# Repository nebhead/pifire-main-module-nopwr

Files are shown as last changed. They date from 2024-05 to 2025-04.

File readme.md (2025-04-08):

# PiFire Main Module PCB (v4.x.x) KiCad Files

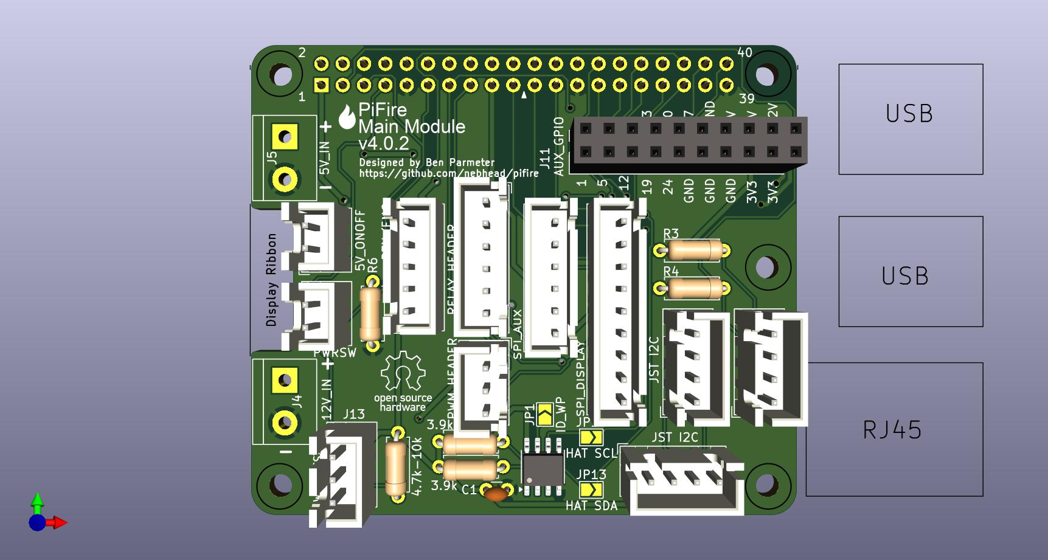
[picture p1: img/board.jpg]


## What is this? 

This PCB provides a modular approach to building your PiFire Smart Smoker Controller.  This board breaks out the many interfaces that are commonly used to support sensors, relays, displays and other devices.  This design allows the user to choose features that suit their needs such as using a PWM DC Fan instead of the AC fan system, or allows for different and expanded probe devices.  Some other notable features are the addition of a 1-Wire bus connector, a wake/shutdown option, and more!  

__Important Notes:__  
1. This board requires v1.8.x of PiFire or later.  As of May 2024, this version is still in development and can be tested by switching to the development branch in the updater page.  Ensure you run through the configuration wizard to select the v4.x.x board and configure your specific settings appropriately. 
1. This board does NOT support the selector switch to run in parallel with the OEM controller.  The pin used for this purpose has been repurposed for the wake/shutdown feature. 

The design intent for this board was to make a DIY accessible PCB that can be more easily put together by the maker/enthusiast of almost any skill level.  Full size components are used in most cases and most (if not all) parts should be readily available to order online.  See the [Interactive BOM](#interactive-bom) for more details about the parts used and links to order.

### What is PiFire? 

PiFire is a SBC based Pellet Smoker Controller.  More details can be found [here](https://nebhead.github.io/PiFire) or [at the GitHub repo](https://github.com/nebhead/pifire). 

## What's in this Repository?

### KiCad Project Files 
In this repository you will find the latest KiCad design files for the  PCB.  Simply load the project file (.kicad_pro) into the KiCad software and you should be able to edit as needed.  Or if you just want to get this board made, jump to the production section below.

### Interactive BOM

There is an interactive BOM located in the [/bom](bom/) folder which details the parts and provides some pin information as well.  Use this to gather the components you may need to build this board out and refer back to it for placement help.    

[BOM + Pin Info](https://nebhead.github.io/pifire-main-module-nopwr)

_This is a standalone HTML file that was autogenerated by the excellent plugin for KiCad. See the plugin here: [https://github.com/openscopeproject/InteractiveHtmlBom](https://github.com/openscopeproject/InteractiveHtmlBom)_

### PDF of the Schematic

Preview the schematic in PDF format here: [Schematic](schematic.pdf)

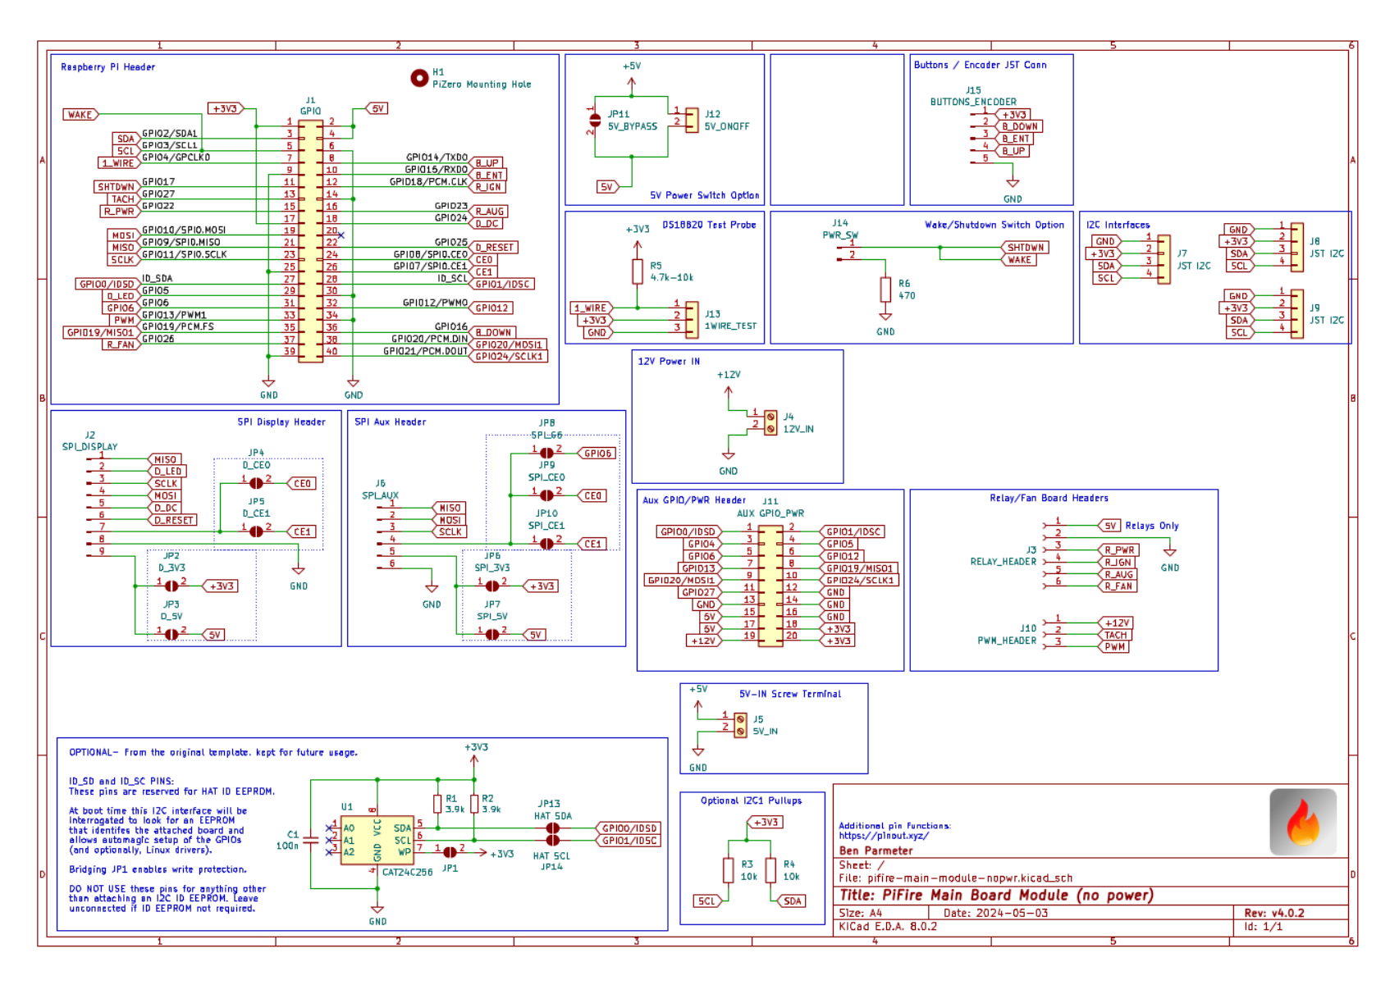
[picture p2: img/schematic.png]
Schematic PNG


### JLCPCB Production Files

If you wish to get these PCBs made by JLCPCB, the production files are provided in the `/production` folder.  For convenience, the file `production.zip` can simply be uploaded to JLCPCB to make it super easy to order boards.

Drop the zip file onto the order page, wait for it to upload then simply continue to order the board.  Optionally, select different board color, PCB quantity, surface finish, etc.  Most of the default settings should be sufficient. 

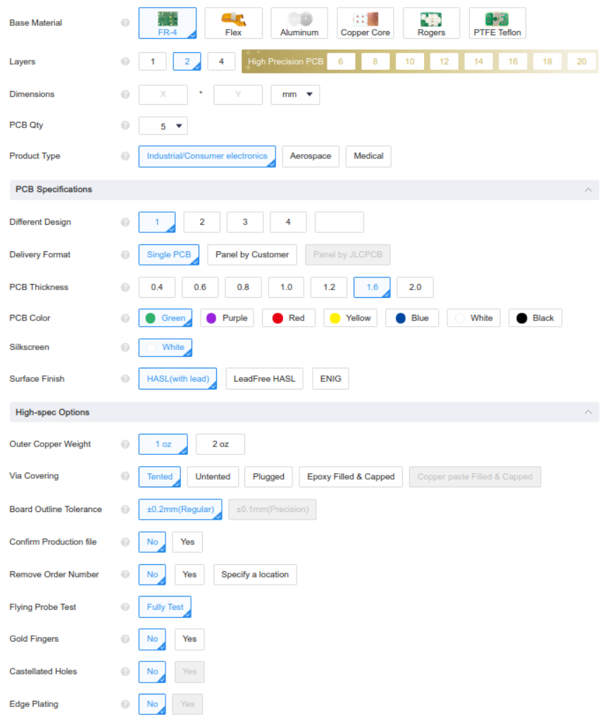
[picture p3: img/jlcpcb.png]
JLCPCB Order Page


### Links to the PCBs in this family of PiFire Boards

This PCB is part of a family of PCBs that can be used together to create  a full PiFire system.  Generally speaking you need the Main Module/Board, a Relay Control Board and a Probe Device board to have a basic PiFire system.  

**Main Module/Board** (required)
* [Main Board v4.0.x](https://github.com/nebhead/pifire-main-module-nopwr)

**Relay/Fan Control Boards** (choose one)
* [Mechanical Relay Module](https://github.com/nebhead/pifire-relay-module)
* [Solid State Relay Module](https://github.com/nebhead/pifire-relay-module-SSR)
* [Solid State Relay + PWM Fan Module](https://github.com/nebhead/pifire-relay-pwm-module-ssr) - Original Design
* [Solid State Relay + PWM Fan Module Alternate](https://github.com/nebhead/pifire-relay-pwm-module-ssr-alt) - Updated Design (Designed with help from @labmonkeyrat on Discord)

**Probe Device Board** (optional)
* [ADS Board](https://github.com/nebhead/pifire-ads-board) 

### General 4.x.x PCB Architecture

Sometimes it is easier to understand how a project is built out by looking at the general architecture.  I've created a high-level diagram of the project so that you can get an idea of how all of this should be connected up. 

The first diagram is of the AC Fan Version of the system.  This version only requires a 5V power supply and only uses a portion of the headers to connect to a relay board.  Technically speaking, in this configuration you could use an off the shelf relay board if you wanted to wire this up yourself.

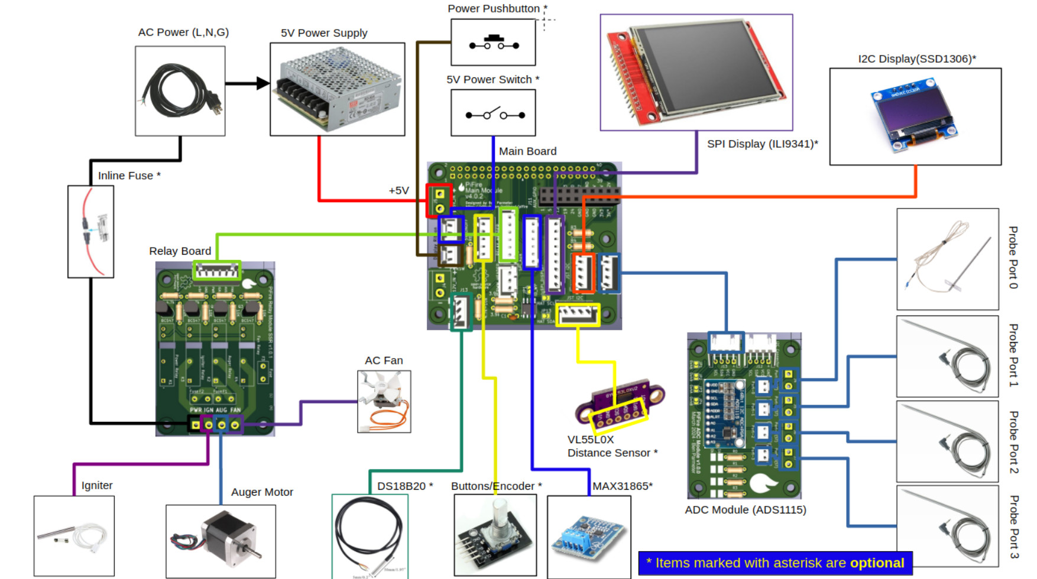
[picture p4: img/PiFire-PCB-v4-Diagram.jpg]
PCB 4.x.x Diagram AC Fan


The second diagram is of the DC PWM Fan version of the system.  You'll notice that this version utilizes a 5V/12V power-supply and the specially design relay/PWM Fan board.  

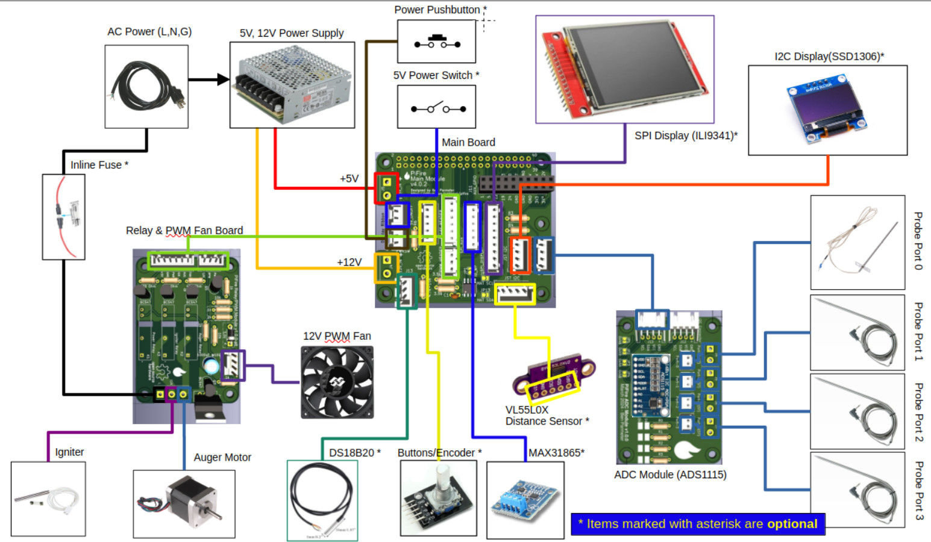
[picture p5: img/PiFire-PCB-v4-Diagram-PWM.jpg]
PCB 4.x.x Diagram DC Fan


### PCB 4.x.x Pinout

Due to space constraints on the PCB silkscreen layer, most of the pins for the JST connectors are unmarked.  Thus I'm providing a handy set of images for the pinout of the major unmarked JST connectors. 

___Buttons & Encoder Header___

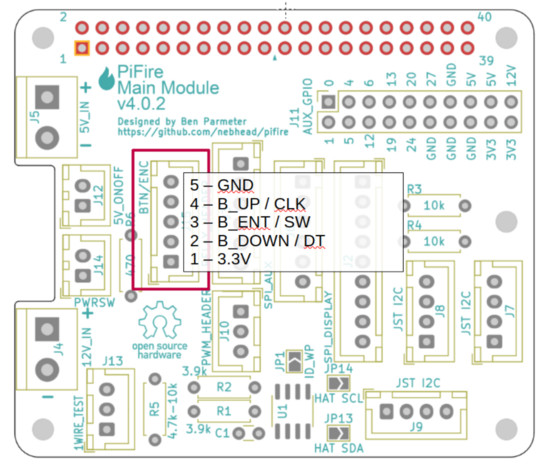
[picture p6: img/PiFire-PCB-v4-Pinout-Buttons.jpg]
PCB 4.x.x Pinout Buttons


___1-Wire Header___ - _Used for the DS18B20 reference probe.  Great for using as a reference to tune your other probes._

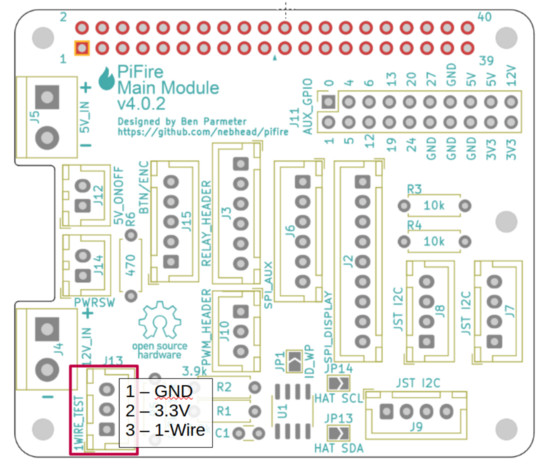
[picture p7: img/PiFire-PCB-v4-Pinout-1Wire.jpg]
PCB 4.x.x Pinout 1-Wire


___Relay and PWM Fan Headers___ - _If you are not using the DC Fan, then only the top header needs to be populated._

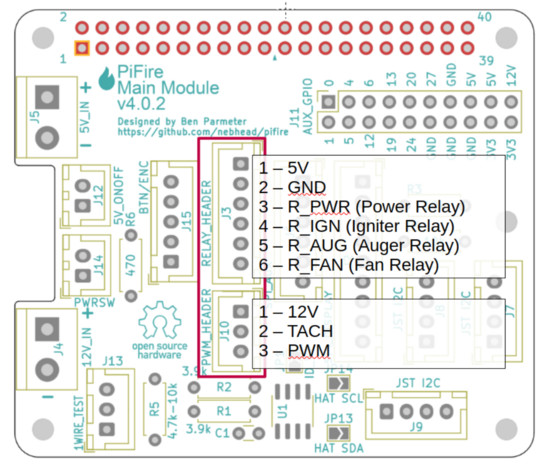
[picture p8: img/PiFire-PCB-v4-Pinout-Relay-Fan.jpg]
PCB 4.x.x Pinout Relay / Fan


___Auxiliary SPI Header___ - _If you are already using the display SPI header, this can be used for another SPI based device such as the MAX38165 RTD probe device._

```note
You must bridge solder jumpers on the back the board to select Chip Enable 0, Chip Enable 1 or GPIO6 (CE0/CE1/GPIO6) and 3.3V or 5V.  Do not bridge both 3.3V and 5V or CE0 and CE1 at the same time or you may damage your system.
```

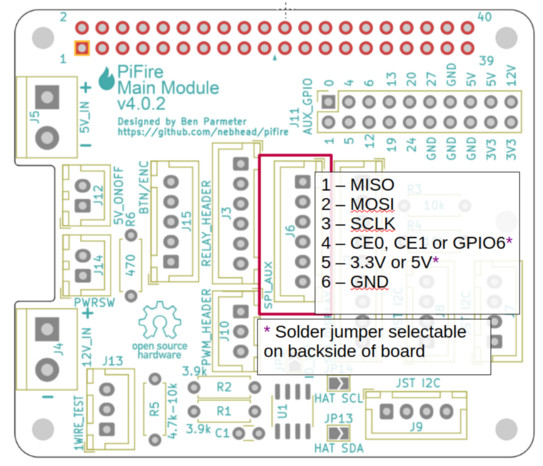
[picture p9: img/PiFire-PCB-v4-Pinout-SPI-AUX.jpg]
PCB 4.x.x Pinout Auxiliary SPI


___Display SPI Header___ - _If you are using a SPI based display like the ILI9341, then this header should match the pinout for that display._

```note
You must bridge solder jumpers on the back the board to select Chip Enable 0 or 1 (CE0/CE1) and 3.3V or 5V.  Do not bridge both 3.3V and 5V or CE0 and CE1 at the same time or you may damage your system.
```

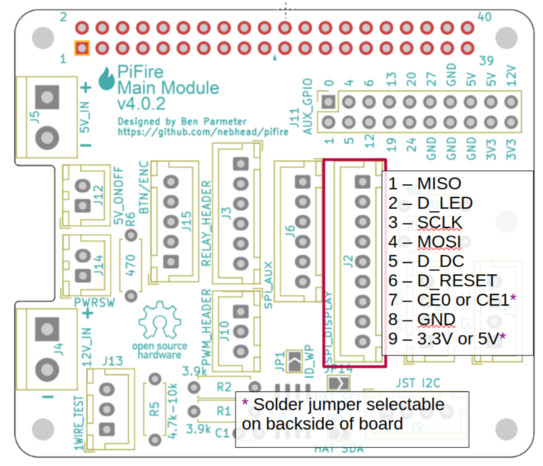
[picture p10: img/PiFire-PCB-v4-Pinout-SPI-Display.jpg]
PCB 4.x.x Pinout Display SPI


___I2C Headers___ - _All of the I2C headers pinouts are identical and can be used for any of the I2C devices including the ADC board, an I2C display, or an I2C distance device._

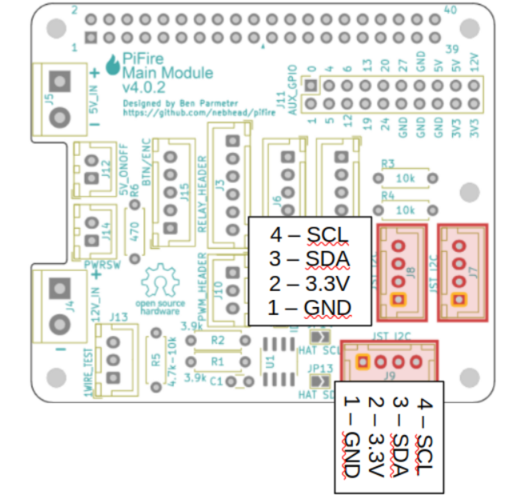
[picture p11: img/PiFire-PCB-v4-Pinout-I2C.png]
PCB 4.x.x Pinout Display SPI


### 3D Printable Enclosures/Boxes 

With all of the 3D Prints for PiFire, a higher temperature filament such as PETG should be used.  PLA generally won't stand up to the temperatures that the components may be exposed to outdoors and near a hot smoker.  

#### Pi Zero W/2W Enclosure

An initial revision of the enclosure for this, supporting the Raspberry Pi Zero W/2W (and may actually also support the Raspberry Pi 3A+ but has not been tested).  The current models should be considered still in development and may have alignment challenges, etc. 

Except for the mounting wings and the Raspberry Pi mounts, the majority of bolts to be used with this enclosure are M3. 

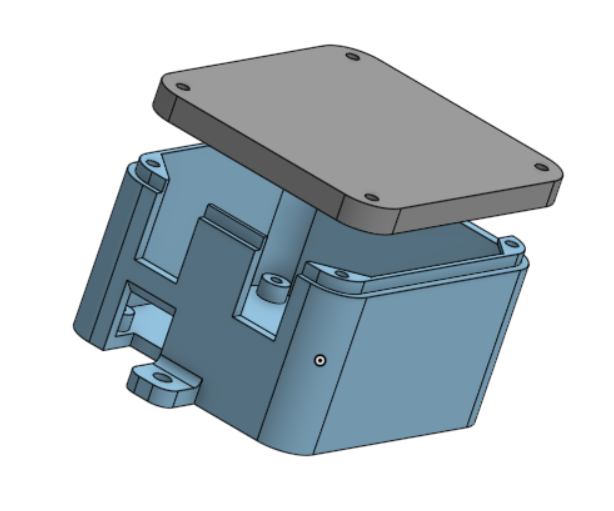
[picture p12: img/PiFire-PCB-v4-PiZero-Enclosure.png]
Pi Zero Enclosure


* STL: [Base](/printables/PiFire-v4-PiZero-Base.stl)
* STL: [Lid](/printables/PiFire-v4-PiZero-Lid.stl)
* OnShape: [Enclosure Original Models](https://cad.onshape.com/documents/3596921e7143afe3464ba577/w/28c0bdfc90c946dc2a56d7d1/e/2ad9de1bc228faf5a8cd0384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)

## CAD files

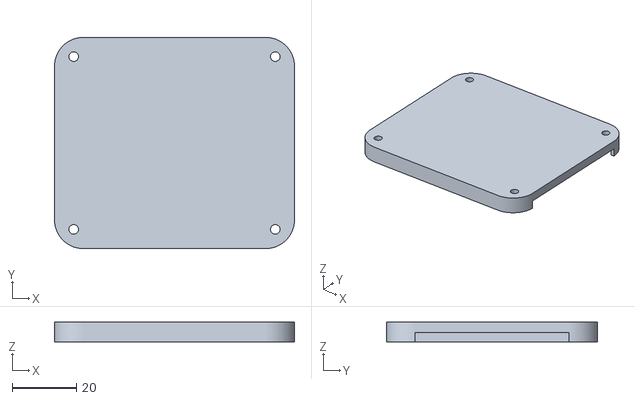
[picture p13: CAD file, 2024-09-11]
printables/PiFire-v4-PiZero-Lid.stl
75.0 x 66.0 x 6.20

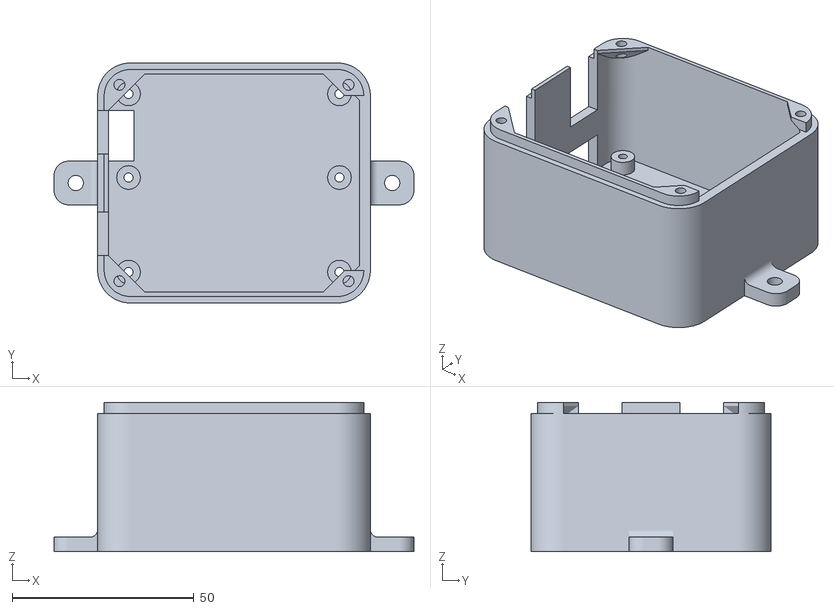
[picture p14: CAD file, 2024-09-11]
printables/PiFire-v4-PiZero-Base.stl
99.0 x 66.0 x 41.0

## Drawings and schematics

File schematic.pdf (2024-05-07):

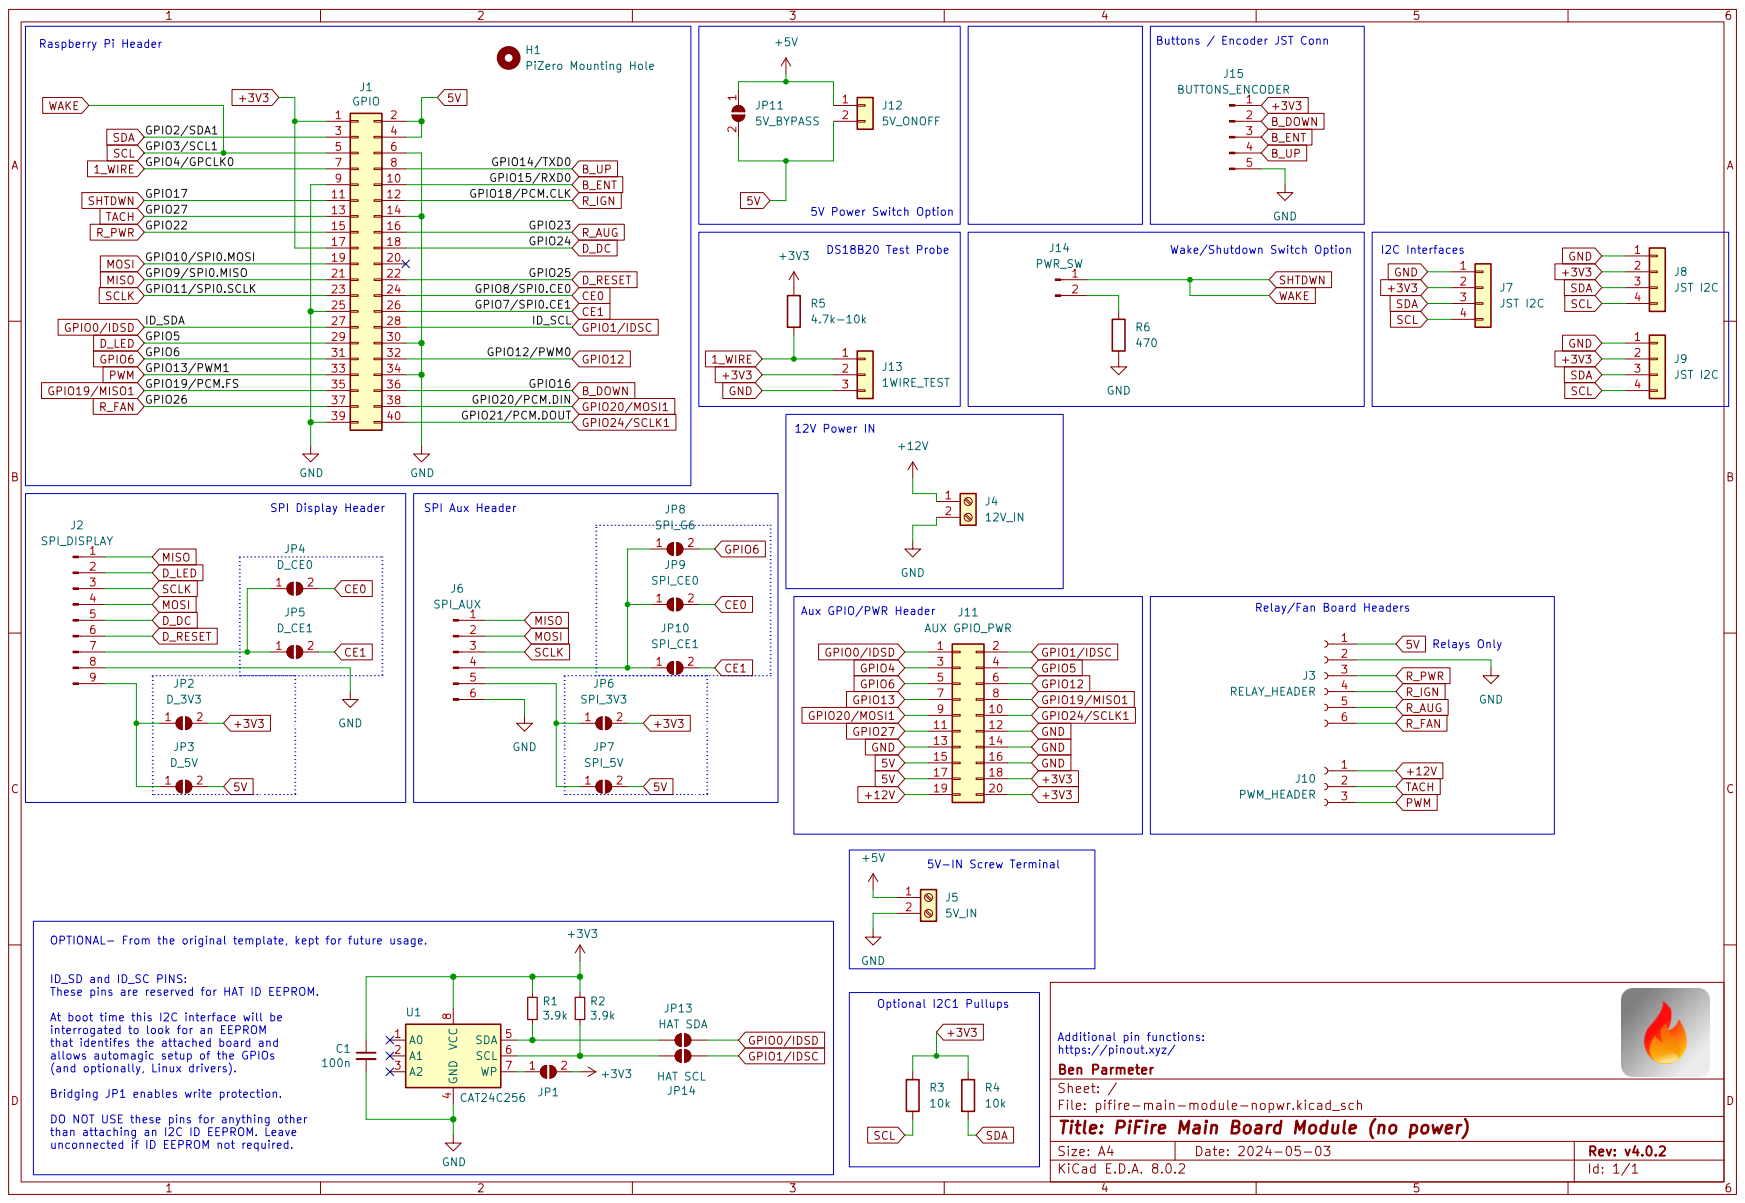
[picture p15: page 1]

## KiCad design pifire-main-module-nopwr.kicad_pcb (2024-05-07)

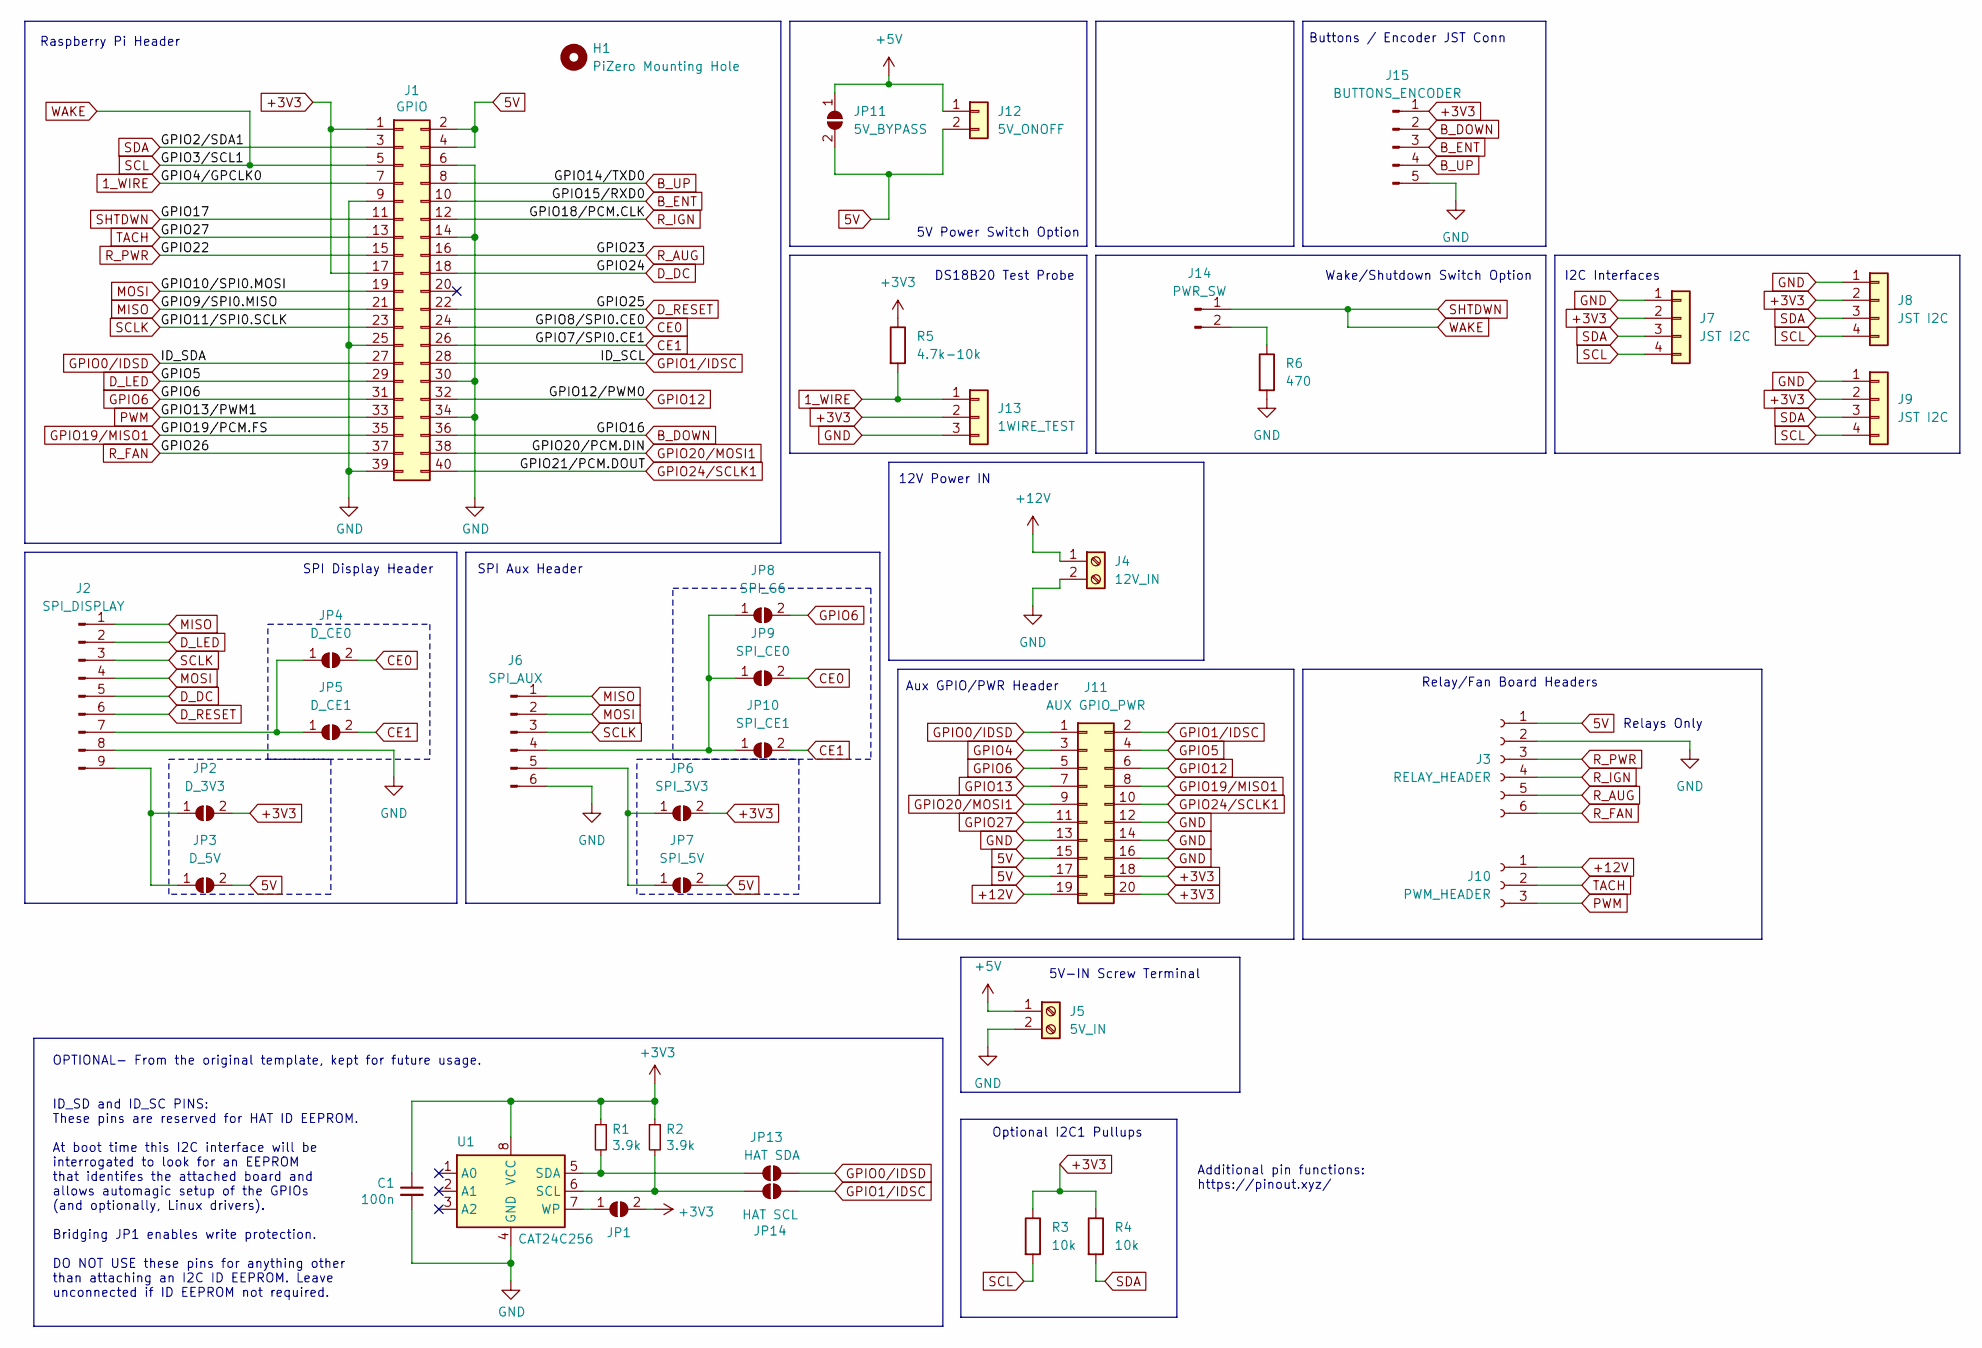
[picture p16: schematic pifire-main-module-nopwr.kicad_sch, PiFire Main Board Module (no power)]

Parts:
C1: 100n; C_Disc_D3.0mm_W1.6mm_P2.50mm
H1: PiZero Mounting Hole; MountingHole_2.7mm_M2.5
J1: GPIO; PinSocket_2x20_P2.54mm_Vertical
J2: SPI_DISPLAY; JST_XH_B9B-XH-A_1x09_P2.50mm_Vertical
J3: RELAY_HEADER; JST_XH_B6B-XH-A_1x06_P2.50mm_Vertical
J4: 12V_IN; TerminalBlock_bornier-2_P5.08mm
J5: 5V_IN; TerminalBlock_bornier-2_P5.08mm
J6: SPI_AUX; JST_XH_B6B-XH-A_1x06_P2.50mm_Vertical
J7, J8, J9: JST I2C; JST_XH_B4B-XH-A_1x04_P2.50mm_Vertical
J10: PWM_HEADER; JST_XH_B3B-XH-A_1x03_P2.50mm_Vertical
J11: AUX GPIO_PWR; PinSocket_2x10_P2.54mm_Vertical
J12: 5V_ONOFF; JST_XH_B2B-XH-A_1x02_P2.50mm_Vertical
J13: 1WIRE_TEST; JST_XH_B3B-XH-A_1x03_P2.50mm_Vertical
J14: PWR_SW; JST_XH_B2B-XH-A_1x02_P2.50mm_Vertical
J15: BUTTONS_ENCODER; JST_XH_B5B-XH-A_1x05_P2.50mm_Vertical
JP1: ID_WP; SolderJumper-2_P1.3mm_Open_TrianglePad1.0x1.5mm
JP2: D_3V3; SolderJumper-2_P1.3mm_Open_TrianglePad1.0x1.5mm
JP3: D_5V; SolderJumper-2_P1.3mm_Open_TrianglePad1.0x1.5mm
JP4: D_CE0; SolderJumper-2_P1.3mm_Open_TrianglePad1.0x1.5mm
JP5: D_CE1; SolderJumper-2_P1.3mm_Open_TrianglePad1.0x1.5mm
JP6: SPI_3V3; SolderJumper-2_P1.3mm_Open_TrianglePad1.0x1.5mm
JP7: SPI_5V; SolderJumper-2_P1.3mm_Open_TrianglePad1.0x1.5mm
JP8: SPI_G6; SolderJumper-2_P1.3mm_Open_TrianglePad1.0x1.5mm
JP9: SPI_CE0; SolderJumper-2_P1.3mm_Open_TrianglePad1.0x1.5mm
JP10: SPI_CE1; SolderJumper-2_P1.3mm_Open_TrianglePad1.0x1.5mm
JP11: 5V_BYPASS; SolderJumper-2_P1.3mm_Open_TrianglePad1.0x1.5mm
JP13: HAT SDA; SolderJumper-2_P1.3mm_Open_TrianglePad1.0x1.5mm
JP14: HAT SCL; SolderJumper-2_P1.3mm_Open_TrianglePad1.0x1.5mm
R1, R2: 3.9k; R_Axial_DIN0207_L6.3mm_D2.5mm_P7.62mm_Horizontal
R3, R4: 10k; R_Axial_DIN0207_L6.3mm_D2.5mm_P7.62mm_Horizontal
R5: 4.7k-10k; R_Axial_DIN0207_L6.3mm_D2.5mm_P7.62mm_Horizontal
R6: 470; R_Axial_DIN0207_L6.3mm_D2.5mm_P7.62mm_Horizontal
U1: CAT24C256; SOIC-8_3.9x4.9mm_P1.27mm

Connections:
1_WIRE: J1.7, J13.1, R5.2
5V: J1.2, J1.4, J3.1, J11.15, J11.17, J12.2, JP3.2 (B), JP7.2 (B), JP11.2 (B)
+3V3: C1.1, J1.1, J1.17, J7.2, J8.2, J9.2, J11.18, J11.20, J13.2, J15.1, JP1.2 (B), JP2.2 (B), JP6.2 (B), R1.1, R2.1, R3.1, R4.1, R5.1, U1.8 (VCC)
+5V: J5.1, J12.1, JP11.1 (A)
+12V: J4.1, J10.1, J11.19
B_DOWN: J1.36, J15.2
B_ENT: J1.10, J15.3
B_UP: J1.8, J15.4
CE0: J1.24, JP4.2 (B), JP9.2 (B)
CE1: J1.26, JP5.2 (B), JP10.2 (B)
D_DC: J1.18, J2.5
D_LED: J1.29, J2.2, J11.4
D_RESET: J1.22, J2.6
GND: C1.2, J1.6, J1.9, J1.14, J1.25, J1.30, J1.34, J1.39, J2.8, J3.2, J4.2, J5.2, J6.6, J7.1, J8.1, J9.1, J11.12, J11.13, J11.14, J11.16, J13.3, J15.5, R6.2, U1.4 (GND)
GPIO0/IDSD: J1.27, J11.1, JP13.2 (B)
GPIO1/IDSC: J1.28, J11.2, JP14.2 (B)
GPIO4: J11.3
GPIO6: J1.31, J11.5, JP8.2 (B)
GPIO12: J1.32, J11.6
GPIO13: J11.7
GPIO19/MISO1: J1.35, J11.8
GPIO20/MOSI1: J1.38, J11.9
GPIO24/SCLK1: J1.40, J11.10
GPIO27: J1.13, J10.2, J11.11
MISO: J1.21, J2.1, J6.1
MOSI: J1.19, J2.4, J6.2
unnamed: J2.7, JP4.1 (A), JP5.1 (A)
unnamed: J2.9, JP2.1 (A), JP3.1 (A)
unnamed: J6.4, JP8.1 (A), JP9.1 (A), JP10.1 (A)
unnamed: J6.5, JP6.1 (A), JP7.1 (A)
unnamed: J14.2, R6.1
unnamed: JP1.1 (A), U1.7 (WP)
unnamed: JP13.1 (A), R1.2, U1.5 (SDA)
unnamed: JP14.1 (A), R2.2, U1.6 (SCL)
PWM: J1.33, J10.3
R_AUG: J1.16, J3.5
R_FAN: J1.37, J3.6
R_IGN: J1.12, J3.4
R_PWR: J1.15, J3.3
SCL: J1.5, J1.11, J7.4, J8.4, J9.4, J14.1, R3.2
SCLK: J1.23, J2.3, J6.3
SDA: J1.3, J7.3, J8.3, J9.3, R4.2

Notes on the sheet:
Relays Only
SPI Display Header
Raspberry Pi Header
Relay/Fan Board Headers
Buttons / Encoder JST Conn
Additional pin functions: https://pinout.xyz/
DS18B20 Test Probe
Aux GPIO/PWR Header
Optional I2C1 Pullups
12V Power IN
I2C Interfaces
ID_SD and ID_SC PINS: These pins are reserved for HAT ID EEPROM. At boot time this I2C interface will be interrogated to look for an EEPROM that identifes the attached board and allows automagic setup of the GPIOs (and optionally, Linux drivers). Bridging JP1 enables write protection. DO NOT USE th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
OPTIONAL- From the original template, kept for future usage.
SPI Aux Header
5V-IN Screw Terminal
5V Power Switch Option
Wake/Shutdown Switch Option

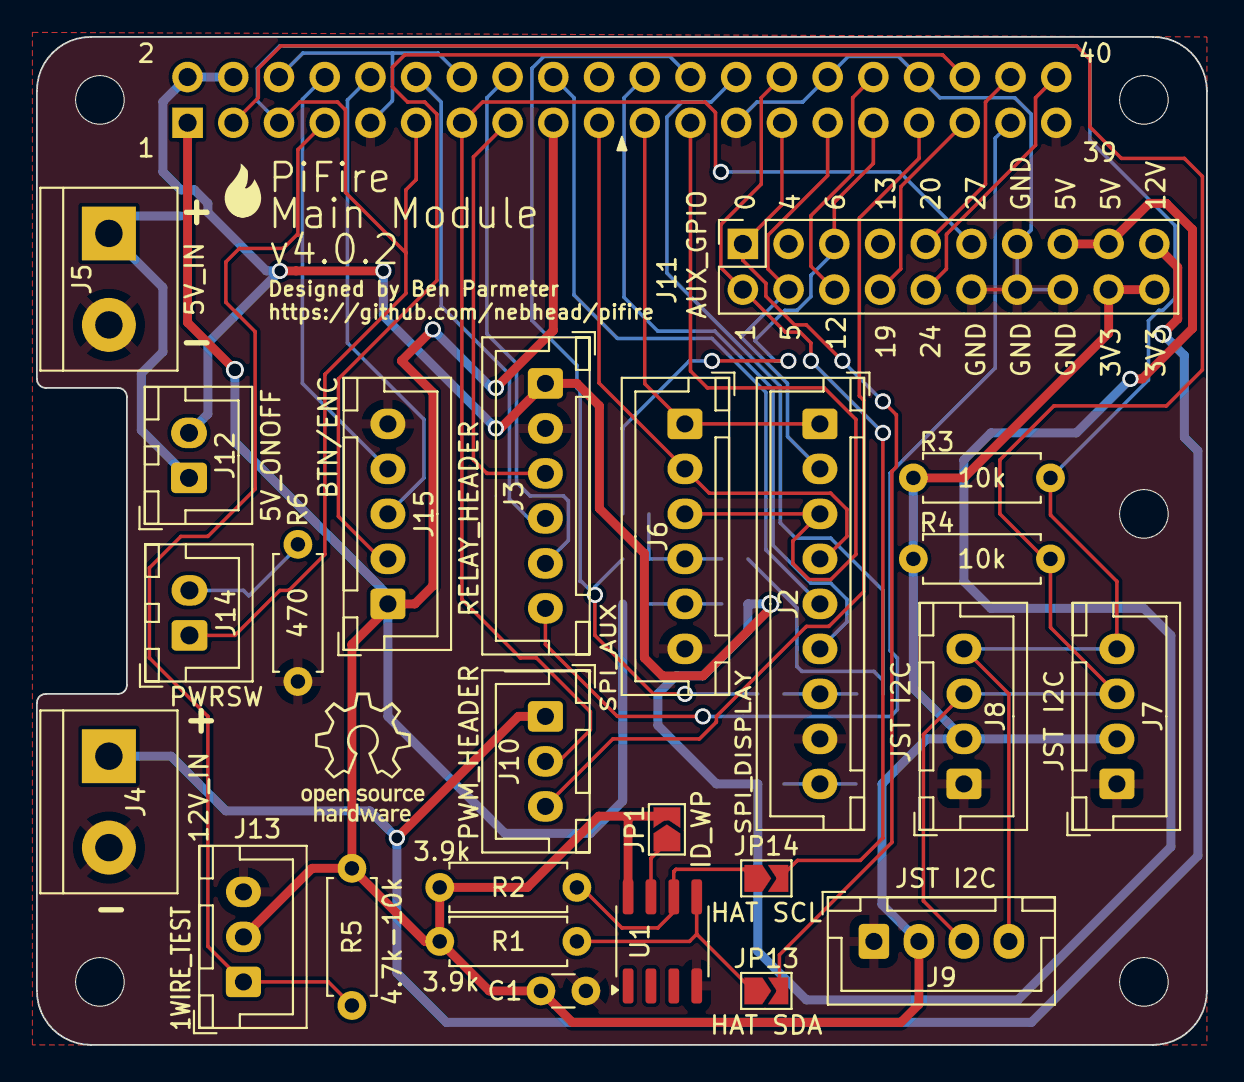
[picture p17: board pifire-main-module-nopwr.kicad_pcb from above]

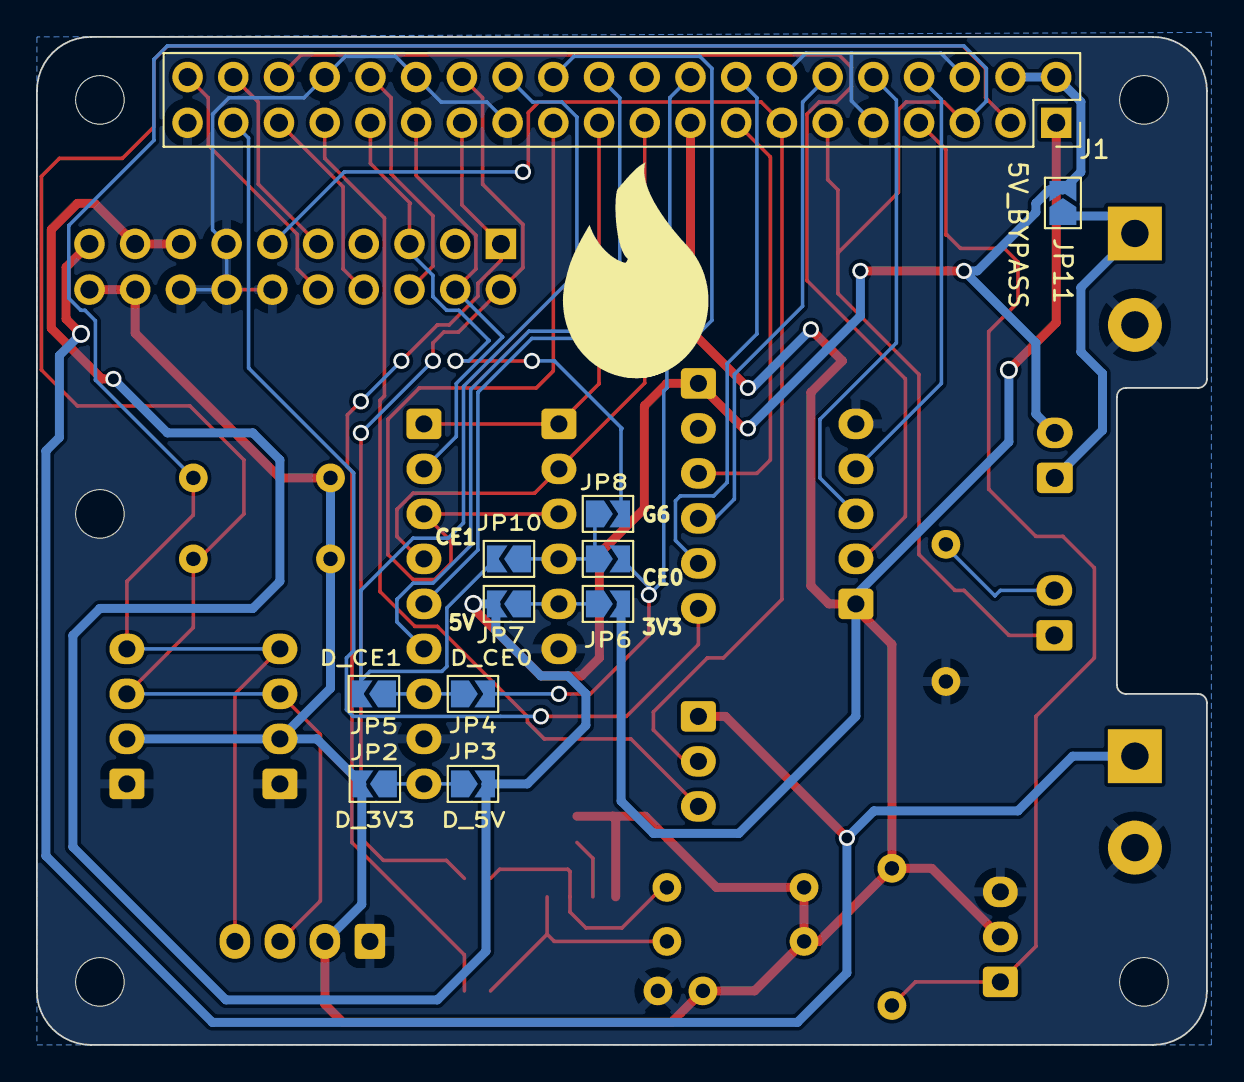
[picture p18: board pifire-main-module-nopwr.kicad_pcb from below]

Board: 2 copper layers, 65.0 x 56.0 mm, 41 parts (11 on the bottom side), 40 nets.

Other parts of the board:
MH1, MH2, MH3, MH4: MountingHole_2.7mm_M2.5

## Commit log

2024-05-07 Updated to v4.0.2
    Split PWM pins out of the Relay/Fan header to create two headers. This makes the board design more modular going forward and makes it easier to source the smaller 6 pin JST header.
    [pifire-main-module-nopwr-B_Cu.gbl, pifire-main-module-nopwr-B_Mask.gbs, pifire-main-module-nopwr-B_Paste.gbp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]
2024-09-07 Update readme.md
    Updating PWM links.
2024-09-11 Added Pinout, High Level Schematic, and 3D Printables
    Added pinout pictures to help with building out cables for external components.
    Added high level schematic to explain where this board fits in the system.
    Added 3D printable files/links for Pi Zero W/2W.
    [PiFire-v4-PiZero-Base.stl, PiFire-v4-PiZero-Lid.stl]
2025-04-08 Updated with I2C pinout image
